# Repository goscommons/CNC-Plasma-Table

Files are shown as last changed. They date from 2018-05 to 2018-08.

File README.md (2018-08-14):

# CNC Plasma Cutter
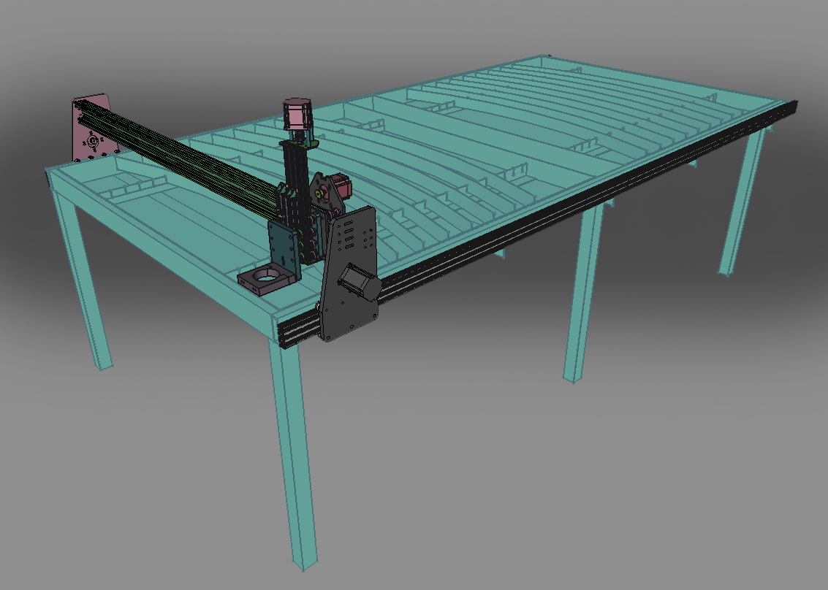
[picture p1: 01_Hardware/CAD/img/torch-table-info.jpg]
Name of the machine

## Purpose of the machine
Many fabricators use plasma arc cutting torches every day, either to replace or complement saws, cut-off wheels, snips, and oxyfuel rigs. Fabricators say the use of this equipment has grown because it can be used in a variety of applications, from installing heating, ventilation, air conditioning, refrigeration, and plumbing systems, to demolishing old industrial wash systems and erecting new ones, to cutting shapes to repair excavator booms or consistently cutting shapes.([Retrieved from the fabricator.com](https://www.thefabricator.com/article/plasmacutting/cut-it-out-how-fabricators-use-plasma-cutters-every-day))
## How the machine works
Plasma cutting is a process that cuts through electrically conductive materials by means of an accelerated jet of hot plasma. Typical materials cut with a plasma torch include steel, Stainless steel, aluminum, brass and copper, although other conductive metals may be cut as well. Plasma cutting is often used in fabrication shops, automotive repair and restoration, industrial construction, and salvage and scrapping operations. Due to the high speed and precision cuts combined with low cost, plasma cutting sees widespread use from large-scale industrial CNC applications down to small hobbyist shops([Retrieved from Wikipedia](https://en.wikipedia.org/wiki/Plasma_cutting)).
### Functional diagram
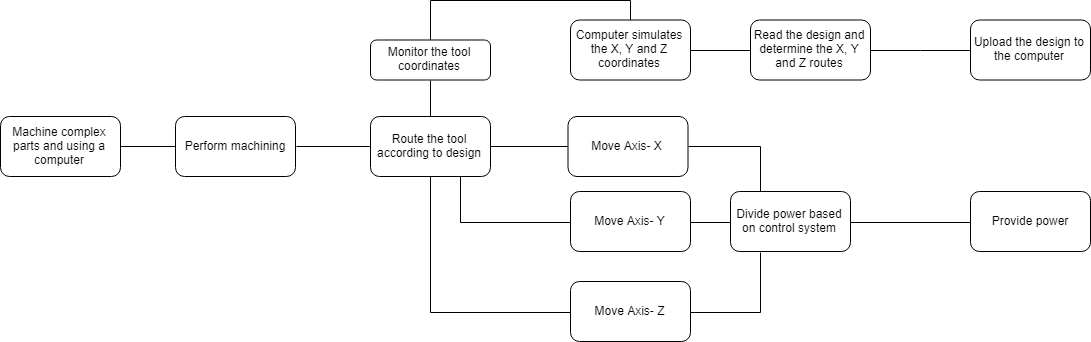
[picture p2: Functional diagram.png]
Fast Diagram- CNC plasma

## Use context
Plasma cutting is most widely used metal plate cutting processes for a large variety of industries. Early plasma cutting systems were used primarily for cutting stainless steel and aluminum plate from 0.5 to more than 6 in. thick. In the last 10 years, developments in plasma cutting technology have come at a fast pace with improved cut quality, automated gas flow control and the CAM software. The latest revision on high-definition machines is their full integration with the CNC machines they are coupled with.
## General specifications
The plasma cutting process needs clean air free of oil, parts and water vapor. The air compressors can leak oil, suck small particles, and they definitely condense water in the tank. Humidity in the compressed air shortens the life of the consumables of the torch. One way to get rig of the humidity is to install in line and air drying refrigerator unit, air filters, desiccants etc.
The one I made is a DIY and can get the job done with a fraction of the cost comparing similar characteristics. 
In general -more into details later-  a 4"PVC pipe right after the compressor exit -(not further downstream, but right after) filled with 1 gallon of reusable desiccant beads will hold all the moisture. The 4" diameter will slow down (bernoulli effect) the air so the beads it will have enough time to absorb the moisture. Also the cold air (due to the difference in pressure as it exits the tank) makes it easier to condense in that 4" pipe. For even better results in hot and humid climates the pipe could be installed in a refrigerator.

## References
1. [FAST diagram](http://www.valueanalysis.ca/fast.php)
2. [Technological evolution of Plasma cutting](https://www.thefabricator.com/article/plasmacutting/the-evolution-of-plasma-cutting)

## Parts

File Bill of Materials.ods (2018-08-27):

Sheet: current
item/part | CAD File | amount | unit | size/specs | cost per unit | shipping | total cost | remarks
Table frame (to be welded)
posts (50*50*3 square steel profile tubes) |  | 6 |  | 3*50*50*800 mm
sides short (25*75*3 rectangular steel profile tubes) |  | 2 |  | 3*25*75*1400 mm
sides long (25*75*3 rectangular steel profile tubes) |  | 2 |  | 3*25*75*3000 mm
cross supports (L profile) |  | 5 |  | (20*20*3)*1455
Water table (simple)
bottom sheet |  | 2 |  | 1400*1400*2 mm
sides (buy 2, cut in half) |  | 2 |  | 2800*75*2 mm
grid holders (T profile Alu with cuts) |  | 4 |  | (25*25*2)*1350 |  |  | Can also be L profile
grid (cutted sheet metal) |  | 18 |  | 20*2*1300
Y-axis (long)
Y-rails linear 20X60 V-slot profile |  | 4 |  | 1500*20*60 mm
timing belt |  | 2 |  | 3100 mm T2.5
timing belt pulley |  | 2 |  | T2.5 |  |  | can be 3D printed if needed.
Stepper motors |  | 2 |  | NEMA23
Y gantry plate |  | 2 |  | from DXF
bearing |  | 2 |  | 625ZZ
M5 lock nuts |  | 8 |  | M5 DIN985
M5 washers |  | 8 |  | M5 DIN 125A
M5 bolts (for motor) |  | 8 |  | M5x30
slide-in nut (to fasten timing belt) |  | 4 |  | ISB type 5- M4
M4 bolts |  | 4 |  | M4*25
screws (to fasten rails to frame) |  | 10
Wheel modules top |  | 8
wheel |  | 1 |  | 23 mm outer
matching ball bearing |  | 1 |  | 5 mm inner
M5 lock nut |  | 1 |  | M5 DIN 985
M5 washer |  | 4 |  | M5 DIN 125A
Spacer |  | 1 |  | 6mm M5
M5 bolt |  | 1 |  | 35 mm / DIN933
Wheel modules below |  | 6
wheel |  | 1 |  | 23 mm outer
matching ball bearing |  | 1 |  | 5 mm inner
M5 lock nut |  | 1 |  | M5 DIN 985
M5 washer |  | 4 |  | M5 DIN 125A
Eccentric spacer |  | 1 |  | 6mm M5
M5 bolt |  | 1 |  | 35 mm / DIN933
X-axis (short/moving)
linear cross bar (40x40 mm T-slot profile) |  | 1 |  | 40*40*1500 mm
M8 Bolts (to fasten cross bar to Y gantry) |  | 2 |  | M8*50
M8 washers |  | 2 |  | M8 DIN 125A
40x80 mm double v-slot U profile rail |  | 1 |  | 40*40*1500 mm
M5 Bolts (to fasten rails to Y gantry) |  | 8 |  | 35 mm / DIN933
M5 washers |  | 8 |  | M5 DIN 125A
timing belt |  | 1 |  | 1600 mm T2.5
slide-in nut (to fasten timing belt) |  | 2 |  | ISB type 5- M4
M4 bolts |  | 2 |  | M4*25
X gantry
X gantry plate front |  | 1 |  | from DXF
X gantry plate back |  | 1 |  | from DXF
Stepper motor |  | 1 |  | Nema23
timing belt pulley |  | 1 |  | T2.5
M5 bolts (for motor) |  | 4 |  | M3x30
M5 lock nuts |  | 4 |  | M3 DIN985
M5 washers |  | 4 |  | M3 DIN 125A
Double wheel modules top |  | 2
wheel |  | 2 |  | 23 mm outer
matching ball bearing |  | 2 |  | 5 mm inner
M5 lock nut |  | 1 |  | M5 DIN 985
M5 washer |  | 9 |  | M5 DIN 125A
Spacer |  | 3 |  | 6mm M5
M5 bolt |  | 1 |  | 35 mm / DIN933
Double wheel modules bottom |  | 2
wheel |  | 2 |  | 23 mm outer
matching ball bearing |  | 2 |  | 5 mm inner
M5 lock nut |  | 1 |  | M5 DIN 985
M5 washer |  | `9 |  | M5 DIN 125A
Eccentric spacer |  | 4 |  | 6mm M5
Spacer |  | 1 |  | 6mm M5
M5 bolt |  | 1 |  | 35 mm / DIN933
nut block for lead screw (anti backlash) |  | 1 |  | 8 screw thread
spacerblocks |  | 2 |  | from STL |  |  | It can be stronge enough from 3D printed PLA right? Otherwise: https://iprototype.nl/products/accessoires/construction/v-slot-spacerblock
Wheel module Z-axis eccentric |  | 4
wheel |  | 1 |  | 23 mm outer
matching ball bearing |  | 1 |  | 5 mm inner
M5 lock nut |  | 1 |  | M5 DIN 985
M5 washer |  | 2 |  | M5 DIN 125A
Eccentric spacer |  | 1 |  | 6mm M5
M5 bolt |  | 1 |  | 35 mm / DIN933
Wheel module Z-axis normal |  | 4
wheel |  | 1 |  | 23 mm outer
matching ball bearing |  | 1 |  | 5 mm inner
M5 lock nut |  | 1 |  | M5 DIN 985
M5 washer |  | 2 |  | M5 DIN 125A
Spacer |  | 1 |  | 6mm M5 |  |  | Shown as eccentric spacers in the CAD file. Needs to be adjusted.
M5 bolt |  | 1 |  | 35 mm / DIN933
Z-axis and gantry
Z-rail 20x60N-O aluminium T-slot profile |  | 1 |  | 20x60x280 mm
horizontal Z gantry plates |  | 2 |  | from DXF
Stepper motor |  | 1 |  | Nema23
Flexible coupling |  | 1 |  | 6,35/8 mm
Lead screw TR8X2 |  | 1 |  | 8*30 mm
Bearing |  | 2 |  | 608ZZ
Lock collar |  | 2 |  | 8 mm
M5 bolt |  | 3 |  | 50
Spacer |  | 3 |  | 40 mm
screws (plates to profile) |  | 6 |  | m5x20
Z-rail 20x60N-O aluminium T-slot profile |  | 1 |  | 20x60x150 mm |  |  | can be cut from a larger rail instead of ordering separate.
90 degrees corner bracket |  | 4 |  | for 20x20 profile
9 mm spacers |  | 4 |  | 9 mm
Mounting plate |  | 1 |  | 3D printed part
Wheel module Z-axis eccentric |  | 3
wheel |  | 1 |  | 23 mm outer
matching ball bearing |  | 1 |  | 5 mm inner
M5 lock nut |  | 1 |  | M5 DIN 985
M5 washer |  | 2 |  | M5 DIN 125A
Eccentric spacer |  | 1 |  | stock
M5 bolt |  | 1 |  | 35 mm / DIN933
Wheel module Z-axis normal |  | 3
wheel |  | 1 |  | 23 mm outer
matching ball bearing |  | 1 |  | 5 mm inner
M5 lock nut |  | 1 |  | M5 DIN 985
M5 washer |  | 2 |  | M5 DIN 125A
Spacer |  | 1 |  | 5,3*10*5 mm
M5 bolt |  | 1 |  | 35 mm / DIN933

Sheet: redesign
item/part | CAD File | amount | unit | size/specs | cost per unit | shipping | total cost | link to store (DUTCH) | remarks
 |  |  |  |  |  |  | €973,64 |  | shipping included?
Table frame
posts (40x40 mm T-slot profile) |  | 6 | ea | 40*40*800 mm | 14,03 |  | €84,18 | https://www.techniek-specialist.nl/aluminiumprofielen-specialist/isb-aluminium-profiel-40x40-eco/
sides short (40x40 mm T-slot profile) |  | 2 | ea | 40*40*1500 mm | 23,94 |  | €47,88 | https://www.techniek-specialist.nl/aluminiumprofielen-specialist/isb-aluminium-profiel-40x40-eco/
sides long (40x40 mm T-slot profile) |  | 2 | ea | 40*40*2000 mm | 31,02 |  | €62,04 | https://www.techniek-specialist.nl/aluminiumprofielen-specialist/isb-aluminium-profiel-40x40-eco/
corner fasteners big |  | 4 | ea | stock | €5,57 |  | €22,28 | https://reprapworld.nl/products/mechanical/frame_components/hoekverbinding_30x60_frame_groot/ | UPDATE
corner fasteners small |  | 12 | ea | stock | €3,25 |  | €39,00 | https://reprapworld.nl/products/mechanisch/frame_onderdelen/hoek_connector_30x30_frame_klein/ | Can also be all big fasteners
cross supports (L profile Alu) |  | 4 | ea | (20*20*2)*1040 | - |  |  | https://metaalcenter.nl/aluminium/aluminium-hoek-profiel/aluminium-hoekprofiel-20-x-20-x-2-mm.html
screws for supports (M5) |  | 8 | ea | stock | €0,12 |  | €0,96 | https://reprapworld.nl/products/mechanical/screws_nuts_and_washers/screws/hex/schroef_m5x20_hex/ | UPDATE
slide nuts for supports (M5) |  | 8 | ea | stock | 6,53/20 pcs |  | €6,53 | https://reprapworld.nl/products/mechanisch/schroeven_moeren_en_ringen/moeren/t_slots/slide_nut_m5_fro_30x30_extrusions_20_pieces/ | UPDATE
rings for supports (M5) |  | 8 | ea | stock | 0,04 |  | €0,32 | https://reprapworld.nl/products/mechanical/screws_nuts_and_washers/washers/sluitring_m5_normaal/ | UPDATE
Water table (simple)
bottom sheet |  | 1 | ea | 2000*1000*2 mm | 58,3 |  | €58,30 | https://metaalcenter.nl/aluminium/aluminium-plaat/aluminium-plaat2000-x-1000-x-2-mm.html | CHECK SIZES FOR 2*1,5 m
sides (sheets, later 1 cut in half) |  | 3 | ea | 2000*30*2 mm | - |  | €21,78 | https://metaalcenter.nl/aluminium/aluminium-plat/aluminium-platstaf-30-x-2-mm.html
grid holders (T profile Alu with cuts) |  | 3 | ea | (25*25*2)*1970 | - |  | €26,13 | https://metaalcenter.nl/aluminium/aluminium-hoek-profiel/aluminium-hoekprofiel-20-x-20-x-2-mm.html | Can also be L profile
grid |  | 11 | ea | 20*2*1000 | - |  | €38,72 | https://metaalcenter.nl/aluminium/aluminium-plat/aluminium-platstaf-20-x-2-mm.html
Y-axis (long)
Y-rails linear 20X60 profile |  | 2 | ea | 2000*20*60 mm | 45,54 |  | €91,08 | https://www.techniek-specialist.nl/aluminiumprofielen-specialist/isb-aluminium-profiel-60x20n-o/ | of https://openbuildspartstore.com/v-slot-20x60-linear-rail/
timing belt |  | 2 | ea | 2100 mm T2.5 | 3,03 |  | €6,06 | https://reprapworld.nl/products/lineaire_beweging/distributieriem_1m_x_5mm_2_5mm_pitch_t2_5/
timing belt pulley |  | 2 | ea | T2.5 | 3,01 |  | €6,02 | https://reprapworld.nl/products/mechanisch/pulleys/aluminium_tandriemschijf_t2_5/ | can be 3D printed if needed.
Stepper motors |  | 2 | ea | - | 12,09 |  | €24,18 | https://reprapworld.nl/products/motors_fans/stepper_motors/nema17_stappenmotor_1_8_stap_4_08_kg_cm/ | Is the torque high enough? Can take the NEMA23: https://reprapworld.nl/products/motoren_fans/stepper_motors/nema23_stepper_motor_1_8_step_12_85_kg_cm/
Y gantry plate |  | 2 | ea | from DXF | - |  |  | Build with DFX file | DXF needs to be adjusted
bearing |  | 2 | ea | 625ZZ | 0,42 |  | €0,84 | https://reprapworld.nl/products/mechanical/bearings/afgeschermde_kogellager_625zz/
M3 lock nuts |  | 8 | ea | M3 DIN985 | 0,04 |  | €0,32 | https://reprapworld.nl/products/mechanisch/schroeven_moeren_en_ringen/moeren/nylon_slot/moer_m3_borgmoer/
M3 washers |  | 8 | ea | M3 DIN 125A | 0,04 |  | €0,32 | https://reprapworld.nl/products/mechanisch/schroeven_moeren_en_ringen/sluitringen/sluitring_m3_normaal/
M3 bolts (for motor) |  | 8 | ea | M3x30 | 0,15 |  | €1,20 | https://reprapworld.nl/products/mechanical/screws_nuts_and_washers/screws/hex/schroef_m3x30_hex/
slide-in nut (to fasten timing belt) |  | 4 | ea | ISB type 5- M4 | 0,22 |  | €0,88 | https://www.techniek-specialist.nl/aluminiumprofielen-specialist/t-sleuf-inschuifmoer/
M4 bolts |  | 4 | ea | M4*25 | 0,12 |  | €0,48 | https://reprapworld.nl/products/mechanical/screws_nuts_and_washers/screws/hex/schroef_m4x25_hex/
slide-in nut (to fasten rails to frame) |  | 10 | ea | ISB type 5- M4 | 0,22 |  | €2,20 | https://www.techniek-specialist.nl/aluminiumprofielen-specialist/t-sleuf-inschuifmoer/
M4 bolts |  | 10 | ea | M4*25 | 0,12 |  | €1,20 | https://reprapworld.nl/products/mechanical/screws_nuts_and_washers/screws/hex/schroef_m4x25_hex/
Wheel modules |  | 14 |  |  |  |  | €40,53
wheel |  | 1 | ea | 23 mm outer | 2,72 |  |  | https://reprapworld.nl/products/mechanisch/kogellagers/625zz_shielded_ball_bearing_23_mm_nylon_wheel/ | CHECK WHETHER THIS IS CHEAPER: https://openbuildspartstore.com/solid-v-wheel-kit/
bearing included |  | 1 | ea | 5 mm inner | -
M5 lock nut |  | 1 | ea | M5 DIN 985 | 0,04 |  |  | https://reprapworld.nl/products/mechanical/screws_nuts_and_washers/nuts/nylon_lock/moer_m5_borgmoer/
M5 washer |  | 4 | ea | M5 DIN 125A | 0,04 |  |  | https://reprapworld.nl/products/mechanical/screws_nuts_and_washers/washers/sluitring_m5_normaal/
Spacer |  | 1 | ea | 5,3*10*5 mm | 0,22 |  |  | https://www.mparts.nl/afstandsbus-rond-ca0158020500 | or https://openbuildspartstore.com/aluminum-spacers-10-pack/
M5 bolt |  | 1 | ea | 35 mm / DIN933 | 0,1 |  |  | https://www.zamro.nl/product/81E0C/d933-rvs-a2-tapbout-m5x35-200
X-axis (short/moving)
linear cross bar (40x40 mm T-slot profile) |  | 1 | ea | 40*40*1500 mm | 23,94 |  | €23,94 | https://www.techniek-specialist.nl/aluminiumprofielen-specialist/isb-aluminium-profiel-40x40-eco/ | I this really needed? Can't it be a thinner profile? For instance a flat 40x20 profile: https://www.techniek-specialist.nl/aluminiumprofielen-specialist/isb-aluminium-profiel-20x40n-o/
M8 Bolts (to fasten cross bar to Y gantry) |  | 2 | ea | M8*50 | 0,22 |  | €0,44 | https://reprapworld.nl/products/mechanisch/schroeven_moeren_en_ringen/schroeven/philips/schroef_m8x30_philips/
M8 washers |  | 2 | ea | M8 DIN 125A | 0,04 |  | €0,08 | https://reprapworld.nl/products/mechanical/screws_nuts_and_washers/washers/sluitring_m8_normaal/
2X 40x40 mm double T-slot profile rail |  | 2 | ea | 40*40*1500 mm | 26,48 |  | €52,96 | https://www.techniek-specialist.nl/aluminiumprofielen-specialist/isb-aluminium-profiel-40x40n-o/ | This is different from the other rails, it has two 20 mm T-slot profile rails next to eachother.
M5 Bolts (to fasten rails to Y gantry) |  | 8 | ea | 35 mm / DIN933 | 0,1 |  | €0,80 | https://www.zamro.nl/product/81E0C/d933-rvs-a2-tapbout-m5x35-200 | included in big pack
M5 washers |  | 8 | ea | M5 DIN 125A | 0,04 |  | €0,32 | https://reprapworld.nl/products/mechanical/screws_nuts_and_washers/washers/sluitring_m5_normaal/
timing belt |  | 1 | ea | 1600 mm T2.5 | 3,03 |  | €3,03 | https://reprapworld.nl/products/lineaire_beweging/distributieriem_1m_x_5mm_2_5mm_pitch_t2_5/
slide-in nut (to fasten timing belt) |  | 2 | ea | ISB type 5- M4 | 0,22 |  | €0,44 | https://www.techniek-specialist.nl/aluminiumprofielen-specialist/t-sleuf-inschuifmoer/
M4 bolts |  | 2 | ea | M4*25 | 0,12 |  | €0,24 | https://reprapworld.nl/products/mechanical/screws_nuts_and_washers/screws/hex/schroef_m4x25_hex/
X gantry
X gantry plate front |  | 1 | ea | from DXF | - |  |  | lasercut updated dxf | DXF needs to be adjusted
X gantry plate back |  | 1 | ea | from DXF | - |  |  | lasercut updated dxf | DXF needs to be adjusted
Stepper motors |  | 1 | ea | - | 12,09 |  | €12,09 | https://reprapworld.nl/products/motors_fans/stepper_motors/nema17_stappenmotor_1_8_stap_4_08_kg_cm/ | Is the torque high enough? Can take the NEMA23: https://reprapworld.nl/products/motoren_fans/stepper_motors/nema23_stepper_motor_1_8_step_12_85_kg_cm/
timing belt pulley |  | 1 | ea | T2.5 | 3,01 |  | €3,01 | https://reprapworld.nl/products/mechanisch/pulleys/aluminium_tandriemschijf_t2_5/
M3 bolts (for motor) |  | 4 | ea | M3x30 | 0,15 |  | €0,60 | https://reprapworld.nl/products/mechanical/screws_nuts_and_washers/screws/hex/schroef_m3x30_hex/
M3 lock nuts |  | 4 | ea | M3 DIN985 | 0,04 |  | €0,16 | https://reprapworld.nl/products/mechanisch/schroeven_moeren_en_ringen/moeren/nylon_slot/moer_m3_borgmoer/
M3 washers |  | 4 | ea | M3 DIN 125A | 0,04 |  | €0,16 | https://reprapworld.nl/products/mechanisch/schroeven_moeren_en_ringen/sluitringen/sluitring_m3_normaal/
Double wheel modules top |  | 2 |  |  |  |  | €13,64
wheel |  | 2 | ea | 23 mm outer | 2,72 |  |  | https://reprapworld.nl/products/mechanisch/kogellagers/625zz_shielded_ball_bearing_23_mm_nylon_wheel/
bearing included |  | 2 | ea | 5 mm inner | -
M5 lock nut |  | 1 | ea | M5 DIN 985 | 0,04 |  |  | https://reprapworld.nl/products/mechanical/screws_nuts_and_washers/nuts/nylon_lock/moer_m5_borgmoer/
M5 washer |  | 9 | ea | M5 DIN 125A | 0,04 |  |  | https://reprapworld.nl/products/mechanical/screws_nuts_and_washers/washers/sluitring_m5_normaal/
Spacer |  | 4 | ea | 5,3*10*5 mm | 0,22 |  |  | https://www.mparts.nl/afstandsbus-rond-ca0158020500
M5 bolt |  | 1 | ea | 35 mm / DIN933 | 0,1 |  |  | https://www.zamro.nl/product/81E0C/d933-rvs-a2-tapbout-m5x35-200 | Depends on the thickness of the plates. This will do up to 3 mm thickness.
Double wheel modules bottom |  | 2 |  |  |  |  | €31,00
wheel |  | 2 | ea | 23 mm outer | 2,72 |  |  | https://reprapworld.nl/products/mechanisch/kogellagers/625zz_shielded_ball_bearing_23_mm_nylon_wheel/
bearing included |  | 2 | ea | 5 mm inner | -
M5 lock nut |  | 1 | ea | M5 DIN 985 | 0,04 |  |  | https://reprapworld.nl/products/mechanical/screws_nuts_and_washers/nuts/nylon_lock/moer_m5_borgmoer/
M5 washer |  | 7 | ea | M5 DIN 125A | 0,04 |  |  | https://reprapworld.nl/products/mechanical/screws_nuts_and_washers/washers/sluitring_m5_normaal/
Eccentric spacer |  | 4 | ea | stock | 2,3 |  |  | https://iprototype.nl/products/accessoires/construction/v-slot-eccentric-spacer
Spacer |  | 2 | ea | 5,3*10*5 mm | 0,22 |  |  | https://www.mparts.nl/afstandsbus-rond-ca0158020500
M5 bolt |  | 1 | ea | 35 mm / DIN933 | 0,1 |  |  | https://www.zamro.nl/product/81E0C/d933-rvs-a2-tapbout-m5x35-200 | Depends on the thickness of the plates. This will do up to 3 mm thickness.
nut block for lead screw (anti backlash) |  | 1 |  | 8 screw thread |  |  | €10,44 | http://vslot-europe.com/home/64-anti-backlash-nut-block-for-8mm-metric-acme-lead-screw.html | Without anti-backlash arm is cheaper and can be bought with other parts: https://iprototype.nl/products/accessoires/construction/8mm-acme-nut-block
spacerblocks |  | 2 |  | from STL |  |  |  | 3D print from STL | It can be stronge enough from 3D printed PLA right? Otherwise: https://iprototype.nl/products/accessoires/construction/v-slot-spacerblock
Wheel module Z-axis eccentric |  | 4 |  |  |  |  | €20,96
wheel |  | 1 |  | 23 mm outer | 2,72 |  |  | https://reprapworld.nl/products/mechanisch/kogellagers/625zz_shielded_ball_bearing_23_mm_nylon_wheel/
bearing included |  | 1 |  | 5 mm inner | -
M5 lock nut |  | 1 |  | M5 DIN 985 | 0,04 |  |  | https://reprapworld.nl/products/mechanical/screws_nuts_and_washers/nuts/nylon_lock/moer_m5_borgmoer/
M5 washer |  | 2 |  | M5 DIN 125A | 0,04 |  |  | https://reprapworld.nl/products/mechanical/screws_nuts_and_washers/washers/sluitring_m5_normaal/
Eccentric spacer |  | 1 |  | stock | 2,3 |  |  | https://iprototype.nl/products/accessoires/construction/v-slot-eccentric-spacer
M5 bolt |  | 1 |  | 35 mm / DIN933 | 0,1 |  |  | https://www.zamro.nl/product/81E0C/d933-rvs-a2-tapbout-m5x35-200 | Check sizing for all bolts with eccentric spacers
Wheel module Z-axis normal |  | 4 |  |  |  |  | €12,64
wheel |  | 1 |  | 23 mm outer | 2,72 |  |  | https://reprapworld.nl/products/mechanisch/kogellagers/625zz_shielded_ball_bearing_23_mm_nylon_wheel/
bearing included |  | 1 |  | 5 mm inner | -
M5 lock nut |  | 1 |  | M5 DIN 985 | 0,04 |  |  | https://reprapworld.nl/products/mechanical/screws_nuts_and_washers/nuts/nylon_lock/moer_m5_borgmoer/
M5 washer |  | 2 |  | M5 DIN 125A | 0,04 |  |  | https://reprapworld.nl/products/mechanical/screws_nuts_and_washers/washers/sluitring_m5_normaal/
Spacer |  | 1 |  | 5,3*10*5 mm | 0,22 |  |  | https://www.mparts.nl/afstandsbus-rond-ca0158020500 | Shown as eccentric spacers in the CAD file. Needs to be adjusted.
M5 bolt |  | 1 |  | 35 mm / DIN933 | 0,1 |  |  | https://www.zamro.nl/product/81E0C/d933-rvs-a2-tapbout-m5x35-200
Z-axis and gantry
Z-rail 20x60N-O aluminium T-slot profile |  | 1 |  | 20x60x280 mm | €8,70 |  | €8,70 | https://www.techniek-specialist.nl/aluminiumprofielen-specialist/isb-aluminium-profiel-60x20n-o/
horizontal Z gantry plates |  | 2 |  | from DXF | - |  |  |  | Aren't there standard parts for this tht we can buy?
Stepper motor |  | 1 |  | Nema23 | 36,3 |  | €36,30 | https://reprapworld.nl/products/motoren_fans/stepper_motors/nema23_stepper_motor_1_8_step_12_85_kg_cm/
Flexible coupling |  | 1 |  | 6,35/8 mm | 4,22 |  | €4,22 | https://reprapworld.nl/products/motoren_fans/couplers/flexible_motor_coupling_6_35_mm_8_mm/
Lead screw TR8X2 |  | 1 |  | 8*30 mm | 9,56 |  | €9,56 | https://reprapworld.nl/products/lineaire_geleiding/spindel_tr8x2_8_mm_2_mm_per_rev_30_cm/
Bearing |  | 2 |  | 608ZZ | 0,75 |  | €1,50 | https://reprapworld.nl/products/mechanisch/kogellagers/afgeschermde_kogellager_608zz/
Lock collar |  | 2 |  | 8 mm | 1,44 |  | €2,88 | http://vslot-europe.com/home/51-lock-collar-8mm.html
M5 bolt |  | 3 |  | 50 |  |  | €3,39 | https://www.gamma.nl/assortiment/gamma-metaalschroef-m5-x-50mm-platkop-verzinkt-15-stuks/p/B458479 | Have to buy in set, nuts included
Spacer |  | 3 |  | 40 mm |  |  | €4,45 | https://iprototype.nl/products/accessoires/construction/v-slot-aluminium-spacer-20mm | cant find 40mm spacers, only when bought per 100 pcs, use 2x20 instead
screws (plates to profile) |  | 6 |  | m5x20 | €0,12 |  | €0,72 | https://reprapworld.nl/products/mechanical/screws_nuts_and_washers/screws/hex/schroef_m5x20_hex/
Z-rail 20x60N-O aluminium T-slot profile |  | 1 |  | 20x60x150 mm | €5,91 |  | €5,91 | https://www.techniek-specialist.nl/aluminiumprofielen-specialist/isb-aluminium-profiel-60x20n-o/ | can be cut from a larger rail instead of ordering separate.
90 degrees corner bracket |  | 4 |  | for 20x20 profile | 3,03 |  | €12,12 | https://reprapworld.nl/products/mechanisch/frame_onderdelen/hoekverbinding_klein_20x20_frame/
9 mm spacers |  | 4 |  | 9 mm | 2,95 /set |  | €2,95 | https://iprototype.nl/products/accessoires/construction/v-slot-aluminium-spacer-9mm
Mounting plate |  | 1 |  | 3D printed part | - |  | ? | These should probably be redesigned to fit the plasmacutter of choice
Wheel module Z-axis eccentric |  | 3 |  |  |  |  | €15,72
wheel |  | 1 |  | 23 mm outer | 2,72 |  |  | https://reprapworld.nl/products/mechanisch/kogellagers/625zz_shielded_ball_bearing_23_mm_nylon_wheel/
bearing included |  | 1 |  | 5 mm inner | -
M5 lock nut |  | 1 |  | M5 DIN 985 | 0,04 |  |  | https://reprapworld.nl/products/mechanical/screws_nuts_and_washers/nuts/nylon_lock/moer_m5_borgmoer/
M5 washer |  | 2 |  | M5 DIN 125A | 0,04 |  |  | https://reprapworld.nl/products/mechanical/screws_nuts_and_washers/washers/sluitring_m5_normaal/
Eccentric spacer |  | 1 |  | stock | 2,3 |  |  | https://iprototype.nl/products/accessoires/construction/v-slot-eccentric-spacer
M5 bolt |  | 1 |  | 35 mm / DIN933 | 0,1 |  |  | https://www.zamro.nl/product/81E0C/d933-rvs-a2-tapbout-m5x35-200 | Check sizing for all bolts with eccentric spacers
Wheel module Z-axis normal |  | 3 |  |  |  |  | €9,48
wheel |  | 1 |  | 23 mm outer | 2,72 |  |  | https://reprapworld.nl/products/mechanisch/kogellagers/625zz_shielded_ball_bearing_23_mm_nylon_wheel/
bearing included |  | 1 |  | 5 mm inner | -
M5 lock nut |  | 1 |  | M5 DIN 985 | 0,04 |  |  | https://reprapworld.nl/products/mechanical/screws_nuts_and_washers/nuts/nylon_lock/moer_m5_borgmoer/
M5 washer |  | 2 |  | M5 DIN 125A | 0,04 |  |  | https://reprapworld.nl/products/mechanical/screws_nuts_and_washers/washers/sluitring_m5_normaal/
Spacer |  | 1 |  | 5,3*10*5 mm | 0,22 |  |  | https://www.mparts.nl/afstandsbus-rond-ca0158020500 | Shown as eccentric spacers in the CAD file. Needs to be adjusted.
M5 bolt |  | 1 |  | 35 mm / DIN933 | 0,1 |  |  | https://www.zamro.nl/product/81E0C/d933-rvs-a2-tapbout-m5x35-200
Electronics (central)
Electric box |  | 1 | ea |  |  |  | €0,00 |  | Can be 3D printed
CNC Hat w/sockets for external drivers |  | 1 | ea |  |  |  | €0,00 | https://www.ebay.com/itm/Raspberry-Pi-CNC-Hat-V2-60-GRBL-v1-1-Compatible-Extra-Options/272596155477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 | Stick with grbl for now. I personally used the "CNC shield" over Arduino but I propose the "CNC Hat" over Raspberry Pi.
Raspberry Pi |  | 1 | ea |  | 40 |  | €40,00
Stepper Drivers TB6600 |  | 1 | 5pack |  | 25,64 | 3,72 | €29,36
wire |  | 20 | meter | 4pin 22awg | 0,8 |  | €16,00 |  | estimation on length
wires for raspberry Pi?? Power,VGA?
Monitor?
Torch Height Control |  | 1 | ea | Proma SD | 238 |  |  | http://proma-elektronika.com/index.php/en/products/thc-torch-height-control/compact-thc-sd

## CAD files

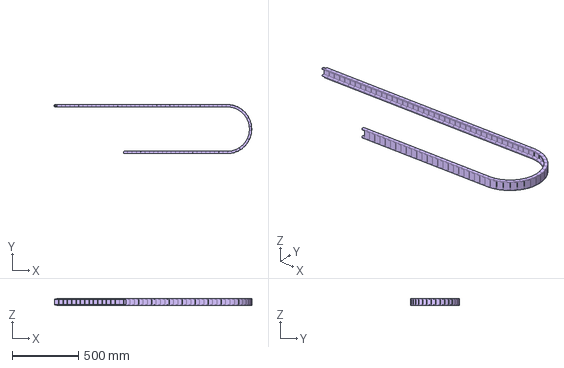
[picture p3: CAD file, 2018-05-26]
01_Hardware/CAD/Chain Assembly Y.fcstd
1491.6 x 371.6 x 49.6 mm

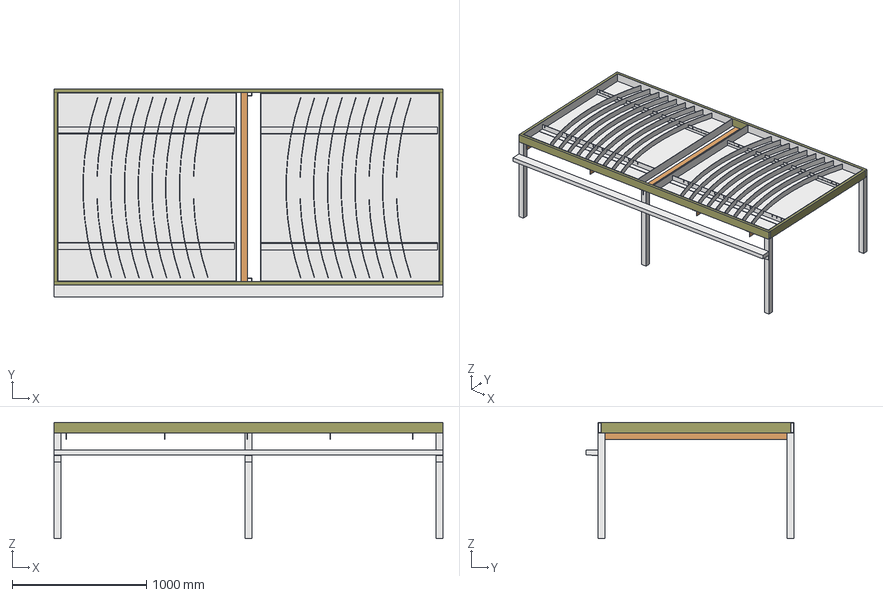
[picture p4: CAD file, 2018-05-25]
01_Hardware/CAD/frame assembly.fcstd
2895.6 x 1544.6 x 864.6 mm
frame sides_01
frame_water_table_cross_supports_01
frame posts_01
Water_table_Assembly_01
Water_table_Assembly_02
Drag_Chain_Y_Axis_Support_Module_01

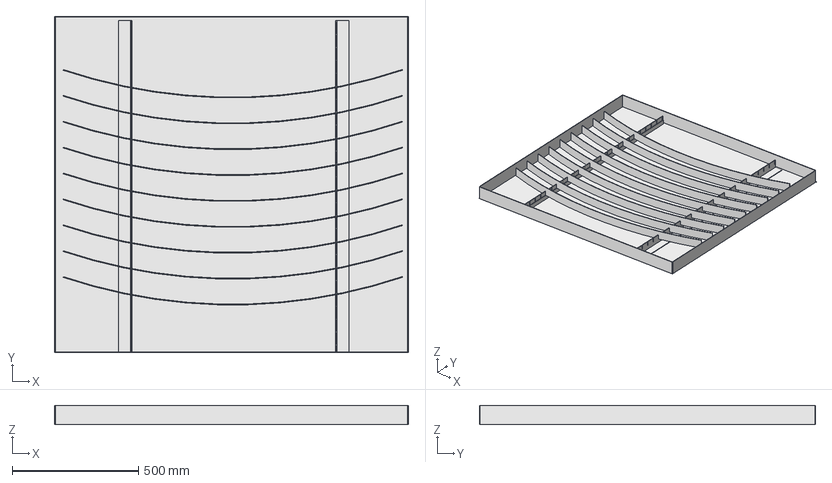
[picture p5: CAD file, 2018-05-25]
01_Hardware/CAD/Water table Assembly.fcstd
1403.3 x 1333.5 x 77.2 mm
water_table_pan_01
water_table_slat_support_01
water_table_slats_01
import_temporary_part

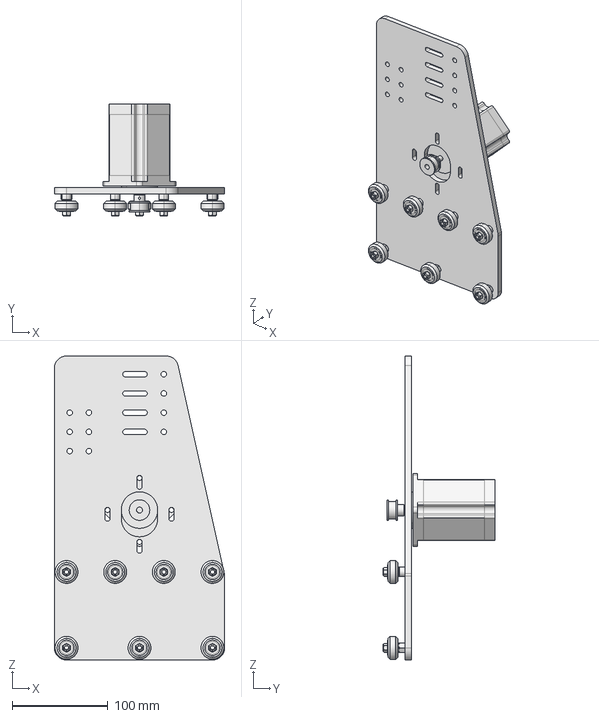
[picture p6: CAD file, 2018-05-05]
01_Hardware/CAD/Y axis gantry assembly MIRROR.fcstd
177.8 x 117.3 x 317.5 mm

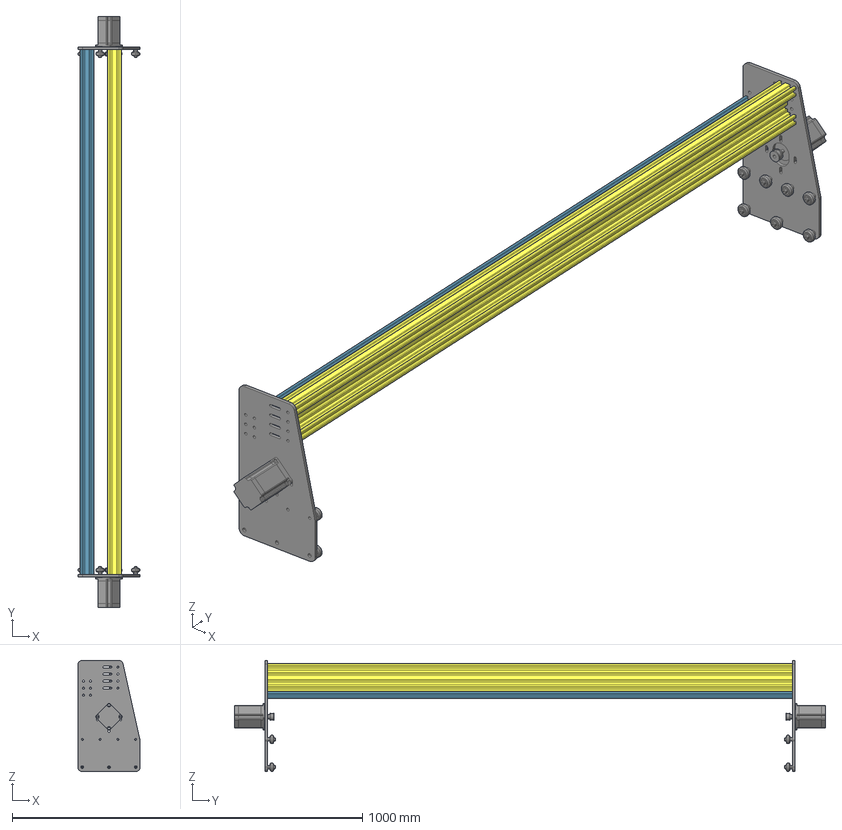
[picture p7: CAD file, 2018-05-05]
01_Hardware/CAD/Y Rail Assembly.fcstd
177.8 x 1687.8 x 317.5 mm
Y_axis_gantry_assembly_01
X Linear rail front
Y_axis_gantry_assembly_MIRROR_01
X Linear Rail Back

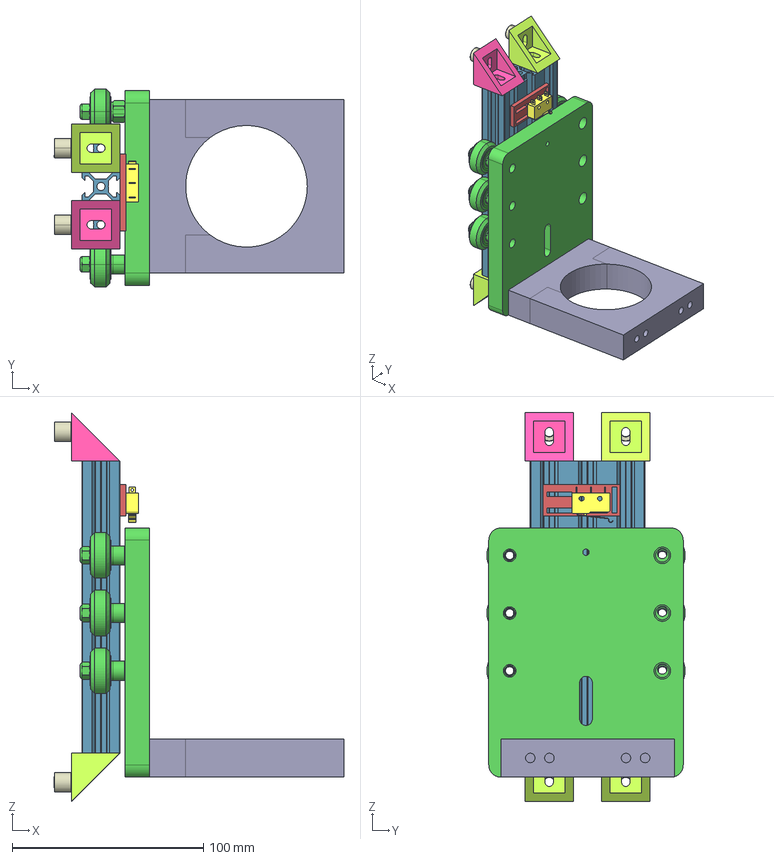
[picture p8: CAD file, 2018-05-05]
01_Hardware/CAD/Z Floating Assembly.fcstd
151.2 x 103.7 x 203.2 mm
Z_Linear_Rail_01
Cast_Corner_Bracket_step1_01
Cast_Corner_Bracket_step1_02
Cast_Corner_Bracket_step1_03
Cast_Corner_Bracket_step1_04
Micro_Limit_Switch_step1_01
End stop mounting plate
Floating_Plate_Module_01
Mount_Plate_02
Aluminum_Spacer_9mm_02
Aluminum_Spacer_9mm_03
Aluminum_Spacer_9mm_04
Aluminum_Spacer_9mm_01

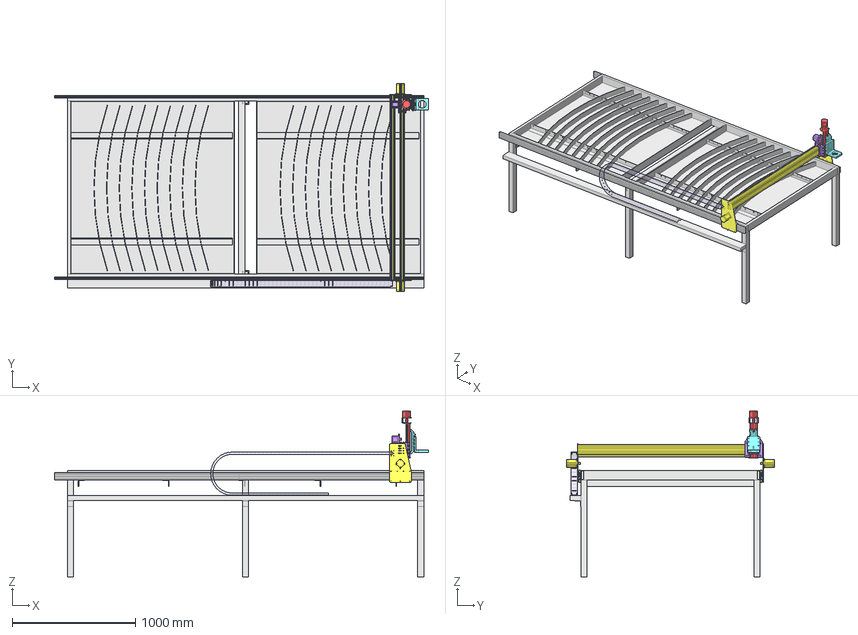
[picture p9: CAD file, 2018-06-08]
01_Hardware/CAD/CNC Master CAD_REMOTE_5589.fcstd
3038.0 x 1687.8 x 1348.3 mm
frame_assembly_01
Y_Linear_Rails_01
X_gantry_01
Y_Rail Assembly
Z_Axis_01
Y_Linear_Rails_02
Z_Floating_Assembly_01001
Chain_Assembly_Y_01

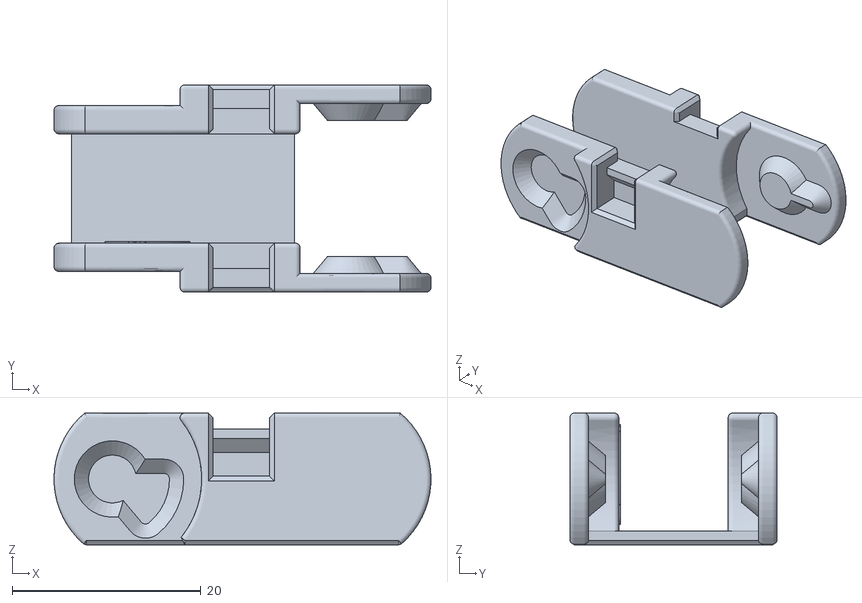
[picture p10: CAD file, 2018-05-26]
01_Hardware/stl-files/UM2CableChain_ChainSegment.STL
40.0 x 22.0 x 14.0

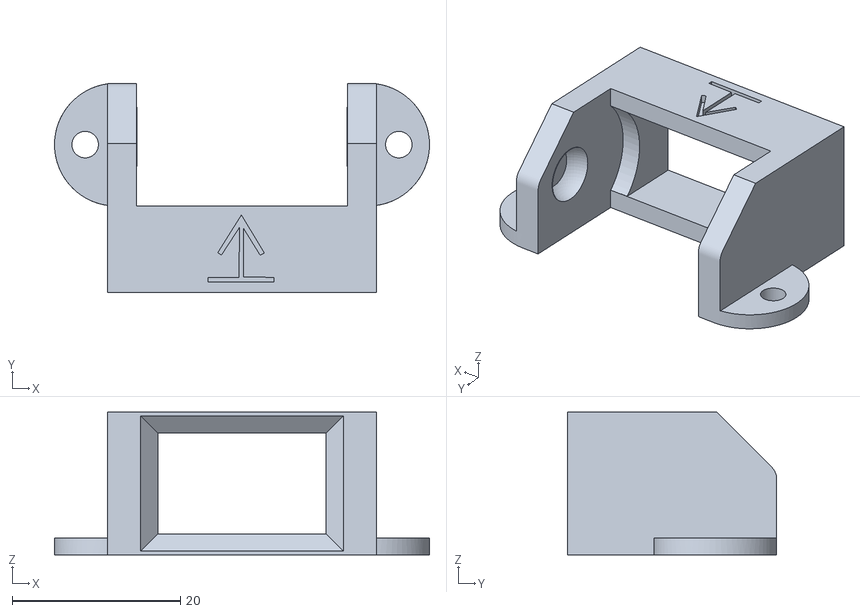
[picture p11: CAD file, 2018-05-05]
01_Hardware/stl-files/HD_Drag_Chain_Start_V2.stl
44.6 x 24.9 x 17.0

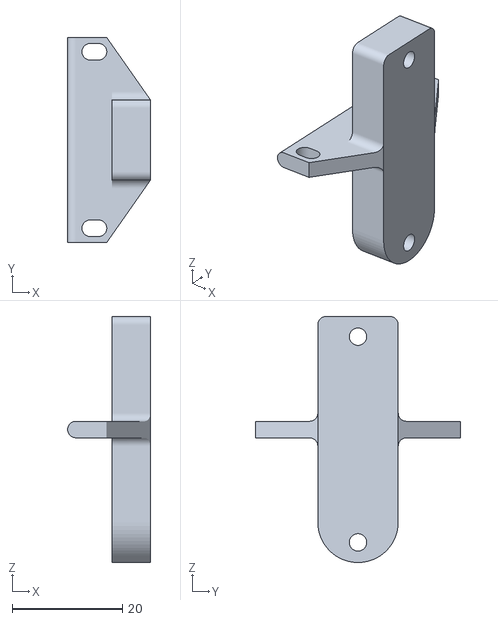
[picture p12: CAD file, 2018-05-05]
01_Hardware/stl-files/N23_Mnt.stl
15.0 x 37.2 x 44.6

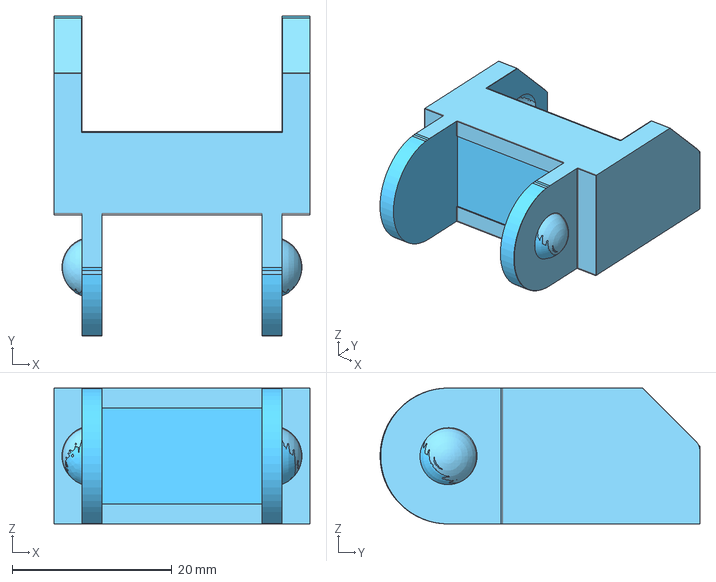
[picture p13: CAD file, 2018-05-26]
01_Hardware/CAD/HD_Drag_Chain_End_V2.FCStd
32.0 x 40.0 x 17.0 mm
HD_Drag_Chain_V2

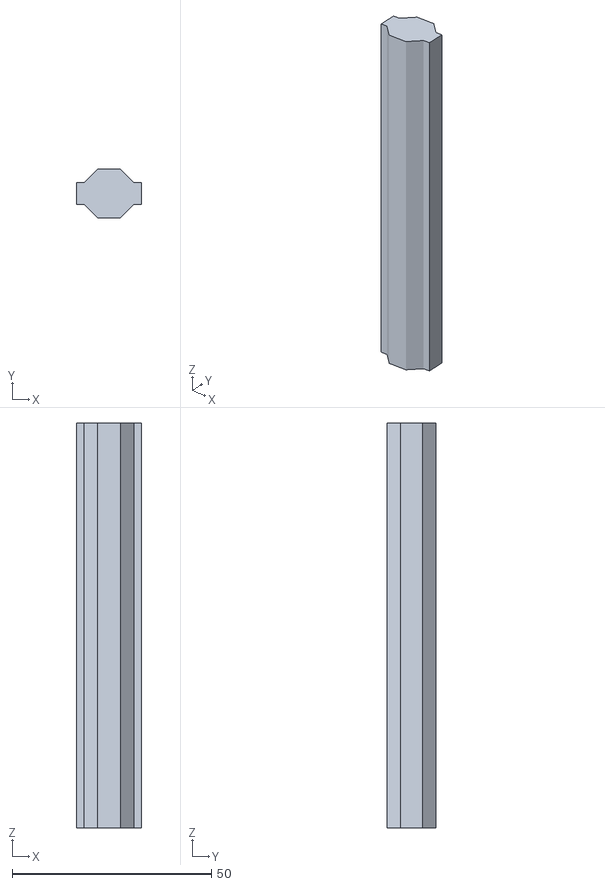
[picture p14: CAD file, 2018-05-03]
01_Hardware/stl-files/rail connector.stl
16.4 x 12.2 x 101.6

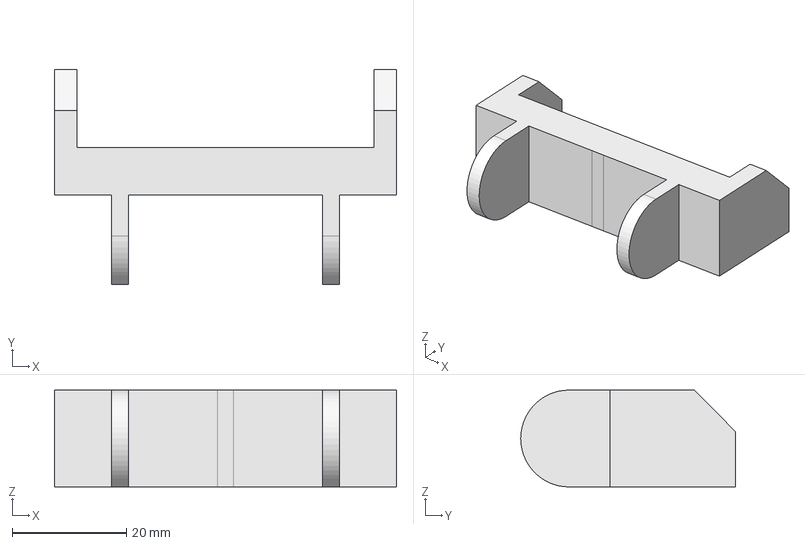
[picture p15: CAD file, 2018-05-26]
01_Hardware/CAD/HD_drag_Chain_V2.FCStd
60.0 x 37.7 x 17.0 mm

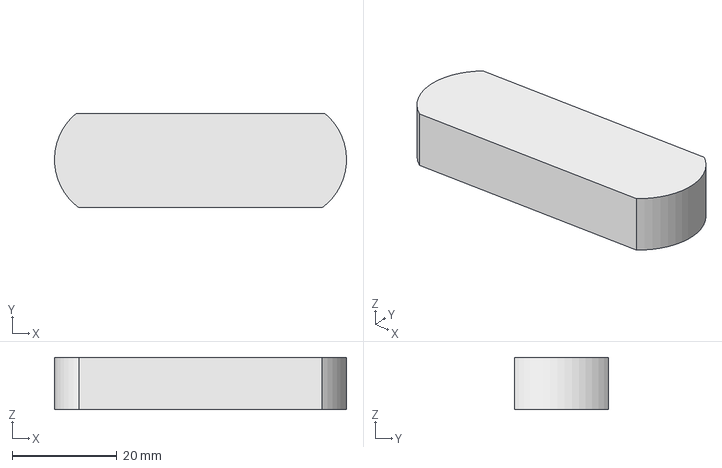
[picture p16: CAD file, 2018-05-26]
01_Hardware/CAD/Cable-chain-chain-segment.FCStd
55.6 x 18.0 x 10.0 mm

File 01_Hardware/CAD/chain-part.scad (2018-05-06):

/* module body(){
	cube()
} */

 cube([18,28,8],true);

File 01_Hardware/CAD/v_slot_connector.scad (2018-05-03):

/*
///////////////////////////////////////////////////////////////////////////////////
// Open SCAD Notes
% = background : # = debug : ! = root : * = disable

union() : intersection() : difference() : minkowski() :hull()
translate([X, Y, Z]) : rotate([X,Y,Z]) : scale([x, y, z])
linear_extrude(height = X, center = true, convexity = 10, twist = Y, slices = 20)

square ([X,Y],center = true) : cube([X, Y, Z], center=true)
circle(r = X) : cylinder(r1=X, r2=Y, h=Z, center=true, $fn=20) : sphere(2, $fn=100)
color("Red",0.7)

polygon(points=[[-50,0],[-50,50],[50,50],[50,0]], paths=[[0,1,2,3]]);
polyhedron(points=[[-50,0],[-50,50],[50,50],[50,0], triangles=[[1,0,3],[2,1,3]]);

// STL Import
translate([0, 0, 0])
import("OpenBeam.stl");

///////////////////////////////////////////////////////////////////////////////////
*/

include <metric_fastners.scad>;


scale = 0.99;
length = 40;


module beam(length=40) {
	linear_extrude(length)
	 polygon([ [-4.5, 0], [-2.7, -1.9], [-5.5,-1.9], [-5.5, -2.8], [-3, -5.7], [3, -5.7], [5.5, -2.8], [5.5,-1.9], [2.7, -1.9], [4.5, 0], [2.7, 1.9], [5.5, 1.9], [5.5, 2.8], [3, 5.7], [-3, 5.7], [-5.5, 2.8], [-5.5,1.9], [-2.7, 1.9] ]);
}


module connector() {
	difference() {
	translate([0, 0, -length/2]) rotate([0, 0, 0]) scale([scale, scale, scale])
 	 beam(length);

*#	translate([0, 2, 0]) rotate([90, 0, 0])
		 cap_bolt_boolean(3, 8, 30);
	}
}



// Primary Placement
translate([0, 0, 0]) rotate([0, 0, 0])
connector(40);

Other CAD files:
01_Hardware/CAD/Y axis gantry assembly.fcstd
01_Hardware/CAD/CNC Master CAD.fcstd
01_Hardware/CAD/Cable-chain-segment.FCStd
01_Hardware/CAD/Drag Chain Y Axis Support Angles.fcstd
01_Hardware/CAD/20 x 40 linear rail Z.fcstd
01_Hardware/CAD/8mm Leadscrew Acme 12in.fcstd
01_Hardware/CAD/Aluminum Spacer .25in.step
01_Hardware/CAD/Aluminum Spacer 20mm.fcstd
01_Hardware/CAD/Aluminum Spacer 9mm.fcstd
01_Hardware/CAD/Aluminum Spacer 9mm.step
01_Hardware/CAD/C beam X rail.fcstd
01_Hardware/CAD/CNC Master CAD_BACKUP_5589.fcstd
01_Hardware/CAD/CNC Master CAD_BASE_5589.fcstd
01_Hardware/CAD/CNC Master CAD_LOCAL_5589.fcstd
01_Hardware/CAD/Drag Chain Y Axis Support Beam.fcstd
01_Hardware/CAD/Drag Chain Y Axis Support Module.fcstd
01_Hardware/CAD/Eccentric Spacer 0.25in.step
01_Hardware/CAD/Floating Plate Module.fcstd
01_Hardware/CAD/Floating Plate.fcstd
01_Hardware/CAD/GT3 Timing Pulley 20T.fcstd
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

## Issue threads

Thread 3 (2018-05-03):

Unused files should be deleted. File tree diagram needed

polemidis, 2018-05-03:
lots of files are not used anymore. One has to open all the sub-assemblies and modules to see what is not used anymore, as find any files that may be missing. (Most likely missing file will be OpenBuillds© cad models).

jurra, 2018-05-22:
This can be closed right?

polemidis, 2018-05-22:
No yet. There is a mess in the files. We need to make a tree diagram (like the one for the grapple) and then  keep the needed files. Most likely there will be deprecated files there.

jurra, 2018-05-22:
Ok I understand

On Tue, May 22, 2018, 12:18 Manolis Karamousas <notifications@github.com>
wrote:

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

Closed 2018-08-21.

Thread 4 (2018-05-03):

The gantry plates have inconsistent width

polemidis, 2018-05-03:
For my initial setup I cut the gantry plates out of ½" plywood out of a CNC router, but plywood has flex and is not proper material for gantry plates.
The cad files have to reverted to the correct width, most likely ¼" which is sufficient for aluminum or garolite material

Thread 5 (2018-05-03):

The table dimensions need adjustment

polemidis, 2018-05-03:
We need to measure the actually cutting area, and depending what size is the parent material, to adjust the table dimensions. In US the minimum sheet metal comes to 4' × 8'

- [ ] Find references of minimimum sheet metal sizes

Either the table has to be longer or the Y rails need to be cut shorter, because they are not of the same length.

Closed 2018-08-21.

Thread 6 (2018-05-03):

Water table dimensions are wrong

polemidis, 2018-05-03:
- [ ] The water tables do not cover the whole bed currently. Make new version with water tables covering the whole bed.
- [ ] The thickness of the material in CAD is wrong, change it. Actual water beds should be made of 14ga not ⅛"

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

Closed 2018-08-21.

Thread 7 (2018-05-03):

Water table improvements

polemidis, 2018-05-03:
- A nice feature will be each bed to have a drain plug so the cutting fluid can be drained to a tank under the plasma table.

- A pump with individual valves for each water table can pump the water from the tank to the tables.

jurra, 2018-08-21:
- [ ] The water tables do not cover the whole bed currently. Make new version with water tables covering the whole bed.
- [ ] The thickness of the material in CAD is wrong, change it. Actual water beds should be made of 14ga not ⅛"

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

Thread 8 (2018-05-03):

Space management under the table

polemidis, 2018-05-03:
The space under the table should be utilized. Equipment that has to go under the table is:

1. The Plasma Cutter
2. The pump
3. The tank
4. A box with electronics for room for the power supply, for stepper drivers in case we need stronger ones, and for the breakout board. (for now the breakout board/stepper drivers are all in one and will be located at the end of the X drag chain on the top of the unused rail from X axis
5. Various tools

Some expanded metal on some 2" × ⅛" angle profiles should suffice.

jurra, 2018-05-22:
It is important to have size reference of equipment that needs to be placed below the table. It would be good to have an idea, and description of the prototype in pictures and examples of final products.

I put an example of plasma industrial plasma cutter
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

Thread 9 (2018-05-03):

Cable drag chains needed

polemidis, 2018-05-03:
The location of the X Axis drag chain is at the top of the 2nd rail at the X axis. CAD is needed

The Y axis drag chain location need to be designed. Most likely right under the right Y rail. but mounts have to be designed

jurra, 2018-05-22:
this one is repeated so I closed it. The other one has more content and comments.

Closed 2018-05-22.

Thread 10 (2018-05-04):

Torch Height Control

polemidis, 2018-05-04:
The Torch Height Control that is used is the [Proma Electronica SD](http://proma-elektronika.com/index.php/en/products/thc-torch-height-control/compact-thc-sd) and costs $300
I am dumb in electronics, but it should be easy to create a THC for a lot less.
The process is something along these lines:
The THC get input of the Arc Voltage of the Plasma, divide it 50:1, to a safe level for electronics, apply some filters, and then generate Step and Dir signals according to the voltage read. To high voltage means that the torch is too high, so step/dir signals that lower the Z axis are needed, and the opposite if too low voltage is measured.
If needed we can fast track this by reverse engineering my THC, or some research for other THC available is needed. There are also various plans on youtube, but are beyond my understanding :( I mean it I do not know much about electronics! :)

polemidis, 2018-05-22:
We can collect any THC resources from the net/youtube, and have them all here. So whoever gets involved with that, will have a better picture of what is needed and how its done by others

Witz0, 2018-08-21:
https://www.aliexpress.com/item/Highly-automated-tracking-Portable300-Arc-Voltage-Torch-Height-Controller-THC-Plasma-Height-Controller/32708675367.html

That is an example of less integrated older style electronics likely for a significantly different system. However, the circuit principles are the same. The separate THC is a good design for safety, modularity, and broad compatibility. The Proma THC manual states it has 1:50 divider, which confused me at first until I realized it is a standard option from the arc source and in addition to another HV divider within the THC itself.

The option from the source is probably better since it probably moves more of the components to the power source and they may be of better quality and give a cleaner signal to start. In that case any voltage divider and filtering on the THC side can be simpler, but this depends on details of that output from the source. Otherwise as the Proma manual states the THC needs HV/HF noise suppression for pilot arc then a HV divider, filtering, an arduino like MC with motor control outputs and optical isolation for safety and signal quality.

Another way may be to create a HV/HF noise suppression-voltage divider RC combo circuit with an opto-isolated ADC that outputs low voltage values back to the main arduino/RsbPi. This simplifies the circuit of the module that must be attached to the arc power supply. A possible con or issue is the arduino or RsbPi may then need to run more software emualtion like the PID currently on the modular THC to take the voltage inputs from the ADC and modify the Z controller outputs. This seems like a better more integrated solution, but grbl is optimized and likely designed to run on its own on the MC. Unless this can be neatly integrated it may cause problems with grbl. I'm currently uncertain of the RspbPi<-->Arduino I/O and if the RsbPi can assist in any way. A faster arduino version could also be an advanced complex option.

I'd guess advantages of moving THC complexity back to the main PCB might be more advanced control of THC functions, more accuracy at higher speeds, varying voltage target more accurately based on cornering speed, and by tracking wear on the consumable. But, given the likely software complexity involved keeping a dedicated MC for THC

Overall one of the most difficult parts is THC circuitry safety. It is critical because of the potential for a failure mode where arc power could enter the CNC side and come in contact with human interfaces. Thorough shielding and proper grounding of all PCB's and cables between them is critical to safety.

jurra, 2018-08-21:
From what I get here @Witz0 we are discussing different architecture options for electronics hardware. It would be nice to have a table to compare. It would be great to outline some requirements that sets criterion to make a proper decision.

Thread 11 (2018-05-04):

Screws have to be added (without threads)

polemidis, 2018-05-04:
All screws have to be added or at least measured in order to be able to provide a BOM

jurra, 2018-05-04:
- [ ] We have to count the screws
- [ ] And classify the different types of screws

polemidis, 2018-05-04:
I propose to replace the Z motor which is a Nema 17, with a Nema 23. The extra torque is not really needed but removes the need for these uncommon M3x45mm. The Nema 23 accepts M5.

jurra, 2018-05-04:
Do you think we are ready to start the BOM, wth the components we have? it would give a rough estimate of the cost right?

polemidis, 2018-05-04:
Yes we could add the more constant expenses leaving the variable ones for the end.
Can you investigate the market in europe for a plasma cutter that is NOT High Voltage, High Frequency start, but is a blowback or striking system pilot start? I do not know that market. If that helps, in the states a suitable plasma cutter which I have and also saw in videos, is the [Harbor Freight one](https://www.harborfreight.com/240-volt-inverter-plasma-cutter-with-digital-display-62204.html) for an entry level, the [Lotos cut60d](http://www.uwelding.com/supreme-cut60d-60amp-digital-control-cnc-non-touch-pilot-plasma-cutter-with-plasma-gouging-function-non-hf-blowback-arc-start-cnc-plasma-cutt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) for a better choice which hac already a 50:1 divider fro the THC, and on Hypertherm for the absolute industry workhorse (for double price :)
Anyway, that comment may be as an different issue for BOL

jurra, 2018-05-04:
Yes will take care of that

On Fri, May 4, 2018, 22:30 Manolis Karamousas <notifications@github.com>
wrote:

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

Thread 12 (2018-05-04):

Y axis Belt relocation?

polemidis, 2018-05-04:
I am wondering if it would be best to relocate the driving belt under the V-Slot® so it will be a) away from dirt and hot sparks. Right now it looks like dirt is piling on top of the belt, and is finding its way between the belt and the v-slot. Once is there is difficult to clean, the belt has to be removed and re-tighten.
That change only needs longer Y gantry plates as the motor will go below.

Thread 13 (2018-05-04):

Belt tightening system

polemidis, 2018-05-04:
Right now in order to tighten the belt these steps has be be followed:
a) the motor bolts have to be loose and the motor at the lowest position
b) the belt secured at the ends
c)the motor pulled up
d) while keeping the motor up, tighten the motor bolts.
But the motor bolts need two hands , one for the nut and one on the head with an allen key.

I propose to redesign the tightening process by making an adapter at the rail ends which will hold the belts tight, and then with a bolt along the long axis (direction of the belt)change the distance of the grabing location.  Its one extra item to be printed but worth the removal of the hassle to tighten the belt

polemidis, 2018-05-25:
This should suffice [](https://www.thingiverse.com/thing:1293079)

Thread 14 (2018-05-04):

Post processor needs to be wrighten

polemidis, 2018-05-04:
The function of the post processor is to add to or change the G-code that the CAM software generates in the specific machine's dialect.
Our CNC Plasma uses the minimal grbl g-code parser, and even though there are widely available post processors for the grbl, code have to be added to facilitate the
a) automatic Z axis zeroing with a floating table
b) ??

polemidis, 2018-05-08:
This is what I use so far.
G17
G90
G38.3 Z-100 F100 ; probing the Z
G0 L20 P1 Z-11 ;distance to raise. It "zeroes" the Z
G0 Z0 ; placing the torch at the Z distance to start firing

M3 S100000 ; ;torch start
G4 P0.6 ; delay, but it needs more

polemidis, 2018-05-09:
The line "G0 L20 P1 Z-11 " above, even though it works, is wrong. The number (-11) is mm (defined in G90) command, and the torch is definitely not 11m above the metal, but 1-2mm. When I troubleshouting the Z axis I messed up the steps/mm, most likely I have to recalculate the stepping

polemidis, 2018-05-22:
Closing this. Sheetcam haw a good post processor

Closed 2018-05-22.

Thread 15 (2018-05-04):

Spring tension to restore floating table

polemidis, 2018-05-04:
I created it in the prototype but have to make it in the CAD   ---Pictures needed---

instead of relying on the weight of the floating table+torch weight, a spring has to restore the floating table for reliability and stress free operation

jurra, 2018-05-22:
This is also a simple task right? finding a proper spring that works for the weight of the torch head. @polemidis correct me if I am wrong.

polemidis, 2018-05-23:
yeah pretty super easy. The weight is actually pulling to the same direction as the spring. But we cannot just count on the weight as dirt/friction etc my not be enough force to keep the torch head down. A small spring will do the job. I am satisfied with the rubber band it just look "cheap to the end user :)

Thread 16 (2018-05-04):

Cable management

polemidis, 2018-05-04:
- [ ] Maybe add to the CAD the Cable chains

- [ ] Design and add to the CAD the support for the Y axis (the long one) cable chain.

- [ ] Replace in CAD the top "threaded rod plate nema 23" (top plate on Z azis) with a longer one so the drag chain can attach there.

jurra, 2018-05-07:
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

jurra, 2018-05-18:
B=50mm width, 18mm height is the ones on the link i believe. Can you open it? The top where you measure the A should be removable so we frst put the wire in, and the close it. It will help 3D printing by a lot since so support is needed.

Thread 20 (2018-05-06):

New breakout board

polemidis, 2018-05-06:
One bottleneck in the assembly process of the machine is the hude delay in crimping wires so they can will have the the "Dupont connectors that the "CNC Shield"  that I use require. Its annoying and takes huge time.
We have to research for a new board that is compatible with the GRBL v1.1 software, and accepts the wires with no connectors, just simple screwed down.

polemidis, 2018-05-08:
One possible alternative is to replace the CNC shield with a similar board but for Raspberry Pi instead the Arduino. That approach even though it looks more expensive is actually a cheaper option as the Rasp. will replace the computer which runs the grbl sender program.
[CNC Board for Raspberry Pi](https://blog.protoneer.co.nz/raspberry-pi-cnc-board-hat/)

jurra, 2018-05-08:
Makes a lot of sense! then the user could talk to the raspberry pi in a home network for instance..

polemidis, 2018-05-09:
I have to double check (never had RPI) but if it can run Freecad, and Sheetcam (maybe the best CAM for plasma out there, in reasonable cost) then you just add a monitor/mouse/keyboard and you have your station ready.

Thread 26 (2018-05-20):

Task breakdown CNC torch table prototyping-testing-redesigning

jurra, 2018-05-20:
## Intro overview:
### We can put here an overview of what are the main tasks for this sprint, what are different problems that need to be solved, etc.  as a summary to guide contributors.

The CNC torch table has some issues that are short term oriented, and others mid term.
We are currently running a prototype test sprint, focused on finished the first working prototype. The sprint includes, the gathering of design recommendations, and updates for the CAD model and design documentation.

### Sprint goals:
1. Finish prototype tests and document enhancements needed
2. Modify the CAD files based on issues shared in the **[sprint board](https://github.com/goscommons/CNC-Plasma-Table/projects/3?fullscreen=true)**

Closed 2018-08-21.

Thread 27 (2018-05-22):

CNC test cut with grapples

jurra, 2018-05-22:
- [ ] What are key success criteria? quality of the cut? @polemidis is good to have a checklist or something that guides the documentation of the test
- [ ] Shut videos of the test

polemidis, 2018-05-22:
To be able to have clear cut pieces.
The variables that affect that is
a) Amperage (but for my low end plasma cutter is at 50Amps. It doesnot go more anyway. Ideally for 1/4" we would need 65Amps)
b) Speed
c) Cutting height
d) Piercing height

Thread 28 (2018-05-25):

Testing-Prototyping documentation of first prototype

jurra, 2018-05-25:
### I quote @polemidis from the chat

There are many things to capture from @polemidis reflections, for now I copied the chat.

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

> Whoever wants to read further, the stepper drivers I am using now, are the DRV 8825. The big drawback is that the user has to tweak their voltage with a screw and the max Amps they could deliver to the stepper motors was 1.5A without a cooling fan, 2.2A with a fan.
> The new ones will be the TB6600. 4Amps easy. No fan is needed, and the motors mount with screw-type connectors. Check them out. They are 10x more expensive than the DRV8825 but their cost is still insignificant $14 from usa, $6 shipped from china

Closed 2018-08-21.

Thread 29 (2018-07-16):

Use as much as possible same structural components (Table and structural parts)

jurra, 2018-07-16:
For the redesign of the table, we can use as much as possible same structural components. Alluminum profiles for the CNC frame and structural parts could be used to also fabricate the table.

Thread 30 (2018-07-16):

Kit Design of CNC Torch Table

jurra, 2018-07-16:
The general overview of the Kit Concept implies the following design goals:

1. To reduce transport costs, by providing the components, and sub-assemblies as compact as possible
2. To facilitate the assembly of the sub-assemblies and components for the user. Make the life easier for those who want to buy a kit and replicate the machine.
3. Make the tool head easy to exchange to convert the design into a router, a CNC laser cutter, or a Plasma cutter.

polemidis, 2018-07-16:
By saying different approach I actually mean complete redesign. Belts are not good enough to that size for router, so we are actually talking for a new machine. We have to clear this issue before continuing. Router is nice thing to have, but do we need it now? Personally I would love to have a router of that size ;) ;) but I have no time now to research a leadscrew type system

jurra, 2018-07-16:
The backlog items can be prioritized, if this is too complicated, or
unfeasible, we can take it to the bottom of the list, otherwise, maybe some
of us can take over this task.

On Mon, Jul 16, 2018 at 7:05 PM, Manolis Karamousas <
notifications@github.com> wrote:

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

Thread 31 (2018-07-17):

Product Backlog Documentation for a Kit design based on the current CNC prototype

jurra, 2018-07-17:
Here we document all the features, improvements and ideas for the new kit design. We are trying out Zenhub to use the scrum workflow.

The backlog may include sketches, ideas, and specific tasks as well.

JannesHN, 2018-07-24:
My idea of a kit of the CNC plasma cutter is that it only contains (relatively) small essential components.
Parts that we can buy in bulk, such as specific stepper motors, the microprocessor, the small elements in the gantries. The rest, the bigger parts such as the frame beams and rods for the x and y axis should be bought locally by the users.

vinaybhajantri, 2018-07-30:
Hey all, please see the general specifications list based on the small scale CNCs in the market. We should be able to determine these for our CNC too.

**Note**: I have already put sample values as an example

1. Standard workable area:  3,850 mm
2. Travelling capacity X axis:  3,850 mm without processing of the ends of profile
3. Travelling capacity Y axis:  350 mm
4. Travelling capacity Z axis:  280 mm
5. Fast feed Y - Z:  max. 30 m/min.
6. Fast feed X axis: 50 m/min.
7. Positioning accuracy: ± 0,1 mm
8. Spindle speed: 1-24,000 r.p.m.
9. Power output router spindle: 7,0 kW S1 with constant feedback torque control       
10. Tool support for 5 tools

jurra, 2018-08-21:
For now lets just keep the current specifications we have in the prototype and put them in the readme. Does it makes sense?

jurra, 2018-08-21:
## restructuring product backlog documentation:
I found many comments in separate issues, that can all be gathered here
Maybe this could also go on a seperate markdown file in the root folder of the repository

## Target requirements for CNC table
To be able to have clear cut pieces.
The variables that affect that is
a) Amperage (but for my low end plasma cutter is at 40Amps. It doesnot go more anyway. Ideally for 1/4" we would need 65Amps)
b) Speed
c) Cutting height
d) Piercing height

## Fabrication requirements
The whole machine should be able to be assembled on site.
This means using stockparts, machining and fastening with the leaast amount of different tools.

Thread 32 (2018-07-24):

BOM of the CNC as it is now

jurra, 2018-07-24:
- Plasma cutter selection related to the board.
- Plasma cutter thickness of sheets. 3mm sheet metals are the most common (Vinay did a check of suppliers in the Netherlands and Germany)
- Cost quality performance  for frames. Specify range of cost efficiency-

Specification range for aquisition of plasma cutter:
- How thick? maxtimum thickness?
- How much affects the range of cost (for frame design but also buying the plasma cutter).

JannesHN, 2018-08-02:
Here is a link to a Google sheet:
https://drive.google.com/open?id=1voFm5NLqLOZ_l4LTmCsCx7BCbBR0maWj1ovEqwTKXfg

It is a dynamic file for collaboration on the Bill of Materials to complete it together.
A static file will be made to keep track of the contributions over time and assure continuity .

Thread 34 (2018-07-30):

Update CAD file with new table frame

JannesHN, 2018-07-30:
When the frame design is updated from welded pieces to a modular design with standard extrusion profiles, a new CAD file must be made

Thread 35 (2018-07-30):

Design modular table frame

JannesHN, 2018-07-30:
A frame that is not a welded piece, but assembled from standard extrusion profiles

jurra, 2018-08-21:
The frame is already designed, is it properly validated?
Is it ready for a merge? or should we have it in the branch of new version that is not yet released?

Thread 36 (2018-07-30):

Grid that allow big and small shapes to be cutted

JannesHN, 2018-07-30:
The grid in the water tables, on which the sheet metals is placed, is decisive for the size of the shapes that can be cutted. Making a finer grid, that might be placed on top of the larger grid, allows for smaller shapes to be cutted by the machine.

polemidis, 2018-07-31:
I do not think so Jannes. The grid is decisive only on the parent material
that will be cut. Finer grid will make the cut more problematic and prone
to failure. I was already considering to remove the flat metals and replace
them with pyramid shapes, but other reasons like availability stopped me
from doing so

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

--
Emmanouil Karamousadakis
Certified Permaculture Designer
AGreekulture Farmstead
Winthrop, ME 04364

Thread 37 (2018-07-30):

Housing for the driver board

JannesHN, 2018-07-30:
In the prototype this is a plastic box. This can be a more tidy box that allows for neat cable management.

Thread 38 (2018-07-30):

Insert timing belt and belt assembly in CAD

JannesHN, 2018-07-30:
It sucks to make. But it will make the CAD design more complete and thus add to the clarity of the information on the design

polemidis, 2018-07-31:
Its not that hard. I already have made similar belt to the 3D printer
design on OSE printer. The only difference is the pitch. If noone else can
do it I will help

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

--
Emmanouil Karamousadakis
Certified Permaculture Designer
AGreekulture Farmstead
Winthrop, ME 04364

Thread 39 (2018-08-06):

Controller: with or without Raspberry Pi

JannesHN, 2018-08-06:
The following discussion took place on the control unit of the machine

**Manolis**
Did we decide? Arduino + CNC Shield or Raspberry Pi + CNC Hat + Monitor (with the later we can have the software already installed)

**Jannes**
Can both drive 4 steppers? Arduino's main benefit will be the price I guess, while the Raspberry Pi is more sturdy and can be more versatile when we start improving the design or adjusting it for other CNC purposes.
My preference goes out to the latter one, but it makes a huge difference in costs.

**Manolis**
Let me explain Jannes. The 1st choice is a CNC shield over an arduino. That has the regular (temporary) -non sturdy wire connections, and requires lots of labor intensive clamping of plugs.
The second choice is a CNC Hat that is running the arduino over a raspberry pi. The raspberry pi plays the role of a computer. Its benefits are that we can have the software already installed, it can be a complete solution as a stand alone CNC machine (no need to connect to another computer), and also has regular screw type connectors that save A LOT of time in clamping of delicate wires, and its more reliable/sturdy. The cost is not that much more, but the offer as a complete standalone system can gives as more money as a better product.

JannesHN, 2018-08-06:
Thanks for the explanation, but that does confirm for me that we should go with the Raspberry Pi included.
We want to shake off the DIY image of the machine, so having a more reliable complete product with the addition of a Raspberry Pi seems obvious.

polemidis, 2018-08-09:
I agree. Raspberry Pi with the CNC Hat, is better solution.

Closed 2018-08-09.

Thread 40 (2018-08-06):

Packaging design for kit

jurra, 2018-08-06:
## References for packaging design
https://www.ups.com/us/en/services/customized-solutions/optimization-logistics/package-engineering.page

jurra, 2018-08-06:
I had some experience with the packaging of a 3D printer kit. Some of the design of this packaging also applies to our context, specially for electronics, and components. They are the most vulnerable components.

## Question?
What about the plasma cutter, do we include it in the package or separatedly?

polemidis, 2018-08-09:
I am leaning towards a separate plasma cutter. different grid voltage/frequency accross the globe is hard to follow. I believe each customer has to buy its own plasma, while we can always suggest the models that we know that work in out countries.

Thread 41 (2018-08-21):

Repo restructuring with proper branches for different designs

jurra, 2018-08-21:
As @Witz0 correctly pointed, there are inconsistencies in documentation, specifically between BOM and current design. This is because the design is being improved, with a new table design that is more modular.

We have directly jumped into the redesign and improvement of the CNC plasma cutter, without clarifying that is a new version with very small change though.

To solve this we can:
- [ ] Merge the changes now (is the design of the new table sufficiently validated @JannesHN ?)
- [ ] Make the branch with v2, and make the changes in BOM for current version.

2nd option takes perhaps an effort that is does not worth it, and maybe we should treat this improvment with @JannesHN as our first official release.

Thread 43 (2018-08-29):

abnormal motions during cutting

Witz0, 2018-08-29:
[Plate with lines instead of arcs](https://files.gitter.im/goscommons-github-io/Lobby/aOJA/IMG_0490.JPG)
From the description it sounds like g-code commands or motion control errors that are inconsistent.

There are many possible causes so tracing this error could be difficult, but especially important if it is an unknown software error that affects all users and requires an issue to be submitted to another repo.

Without extensive knowledge of these systems, I can only think of a few possible causes from previous reading; mostly from the grbl wiki pages and issues:
https://github.com/gnea/grbl/wiki/Known-Issues

- Most likely is electrical interference, which can be chaotic in nature.
  - The [grbl repos](https://github.com/gnea) have many CNC builders' comments about such issues and it is especially significant on plasma systems due to the arc noise.
  - Reviewing [design issues photos](https://github.com/goscommons/CNC-Plasma-Table/tree/master/00_Design_Issues) shows some wiring details and the plastic boxes used to house the electronics.
  - The plastic is great for prototype work since it isolates potential shorts and is easy to rework. However, it also offers little or no shielding like metal would.

  - From the photos, it is unclear exactly what kind of cables and wires are used, but it does not appear to be shielded (poly fiber strands for riser cable type strain relief are visible).
    - Types of exterior grade plenum rated cables with foil shield and drain/ground wire are ideal for data signals outside a metal box.
      - Other considerations are twisted pair (TP) for differential signals (to THC),  stranded (patch) cable for flexibility;
      - unshielded cable with solid core wires can be used for jumpers between PCB's in screw terminals, but need to be in a shielded box;
      - Some Cat6 has plastic spline spacer (flexibility?) and Cat7 has separately shielded pairs.

  - Considering Pros/Cons of designs using a metal box for electronics may be critical.

    - A soild metal box should act as a faraday cage offering good shielding.
    - If used as chassis ground for electronics it must always be isolated from the + (plasma system ground) work circuit, which the table is apart of. User error such as bridging with metal parts is a potential problem.
    - Heat dissipation for a sealed metal box should be considered.
    - A metal box near the table but isolated from it could act as a fairly complete user interface.

- Next, see [USB serial transmission errors](https://github.com/gnea/grbl/wiki/Known-Issues#usb-to-serial-transmission-errors) in arduino clones and some official Arduinos the USB serial chip has bugs; the official ones have a firmware fix.

- Another common noise issue that introduces motion errors is [Wiring Limit Switches](https://github.com/gnea/grbl/wiki/Wiring-Limit-Switches). Many users add optically isolated limit switches to prevent noise from motors or plasma arcs feeding back as well as better software debouncing.

- A less likely issue now is incorrectly manufactured USB cables. A quick multimeter continuity test between both ends of the exterior plug chasis will tell if they bonded the sheilding to the cable ends correctly.
- Also, useful to know [arduino USB](http://forum.arduino.cc/index.php?topic=27226.msg201939#msg201939) spec appears to be v1.1 with max cable lengths of 9.8ft.

A good way to dry run the CNC system to test these errors would be ideal. Disabling the arc would be step one, but video of motions may be insufficient. Maybe a crude plotter (sprung pen/pencil) attachment could be (3D printed?) added to test g-code motions on paper taped to a metal sheet, but I'd guess this would require some software changes as well so expected signals can be ignored.

polemidis, 2018-08-29:
Its not a shielding problem. I am positive. I detected abnormal behavior only when there is a G2 movement (command "G2" on the g-code)
Statistically speaking it would be extremely rare to show up only in G2 moves (these are arcs).

But despite that, shielding is something we have to incorporate into the build, since it will eliminate possible errors to users. Its good to know that right now with unshielded wires, I have not noise in the machine, so one extra step in shielding will make 1000%  sure that we will never have to deal with that issue.

The solution to the G2 commands is either
a) tell the g-code generating software (sheetcam )to not use them
b) tell the g-code sender(universal Gcode sender) to transform the g2 arcs into small G1 straight lines before it sends it to the board
c) fine tune the accuracy on the Sheetcam. I have to experiment with the decimal points, and the rounding that is happening at some point.
d) make sure that Sheetcam uses the "Center Format Arc" rather than the "Radius Format"
[http://linuxcnc.org/docs/html/gcode/g-code.html#gcode:g2-g3](url)

The c) or/and d) looks like the proper way as the b) adds too much load to the processor and the a)also adds huge amounts of code.

jurra, 2018-08-29:
@Manolis Karamousadakis <polemidis@gmail.com> it would be also nice to
explain to Abe the difficulties you had wen using other open source
solutions. This is an issue that I don't know if is open in the repo at the
moment. But you basically went for sheetcam, to validate the hardware
design. The issue of finding an open source solution that works is still
open I guess.

On Wed, Aug 29, 2018 at 12:44 PM Manolis Karamousas <
notifications@github.com> wrote:

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

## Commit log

2018-05-03 Initial commit. Some files are deprecated
    [20 x 40 linear rail Z.fcstd, 8mm Leadscrew Acme 12in.fcstd, C beam X rail.fcstd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]
2018-05-04 added missing parts, but some assemblies broke need re-establishment
    [Aluminum Spacer .25in.step, Aluminum Spacer 20mm.step, Aluminum Spacer 9mm.step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]
2018-05-05 work on floating plate
    [Aluminum Spacer 20mm.fcstd, Aluminum Spacer 20mm.step, Aluminum Spacer 9mm.fcstd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]
2018-05-05 cable chain files added not yet in master cad
    [HD_Drag_Chain_End_V2.stl, HD_Drag_Chain_Start_V2.stl, HD_Drag_Chain_V2.stl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]
2018-05-05 housekeeping of the Y Rail Assembly
    [C beam X rail.fcstd, CNC Master CAD.fcstd, GT3 Timing Pulley 20T.fcstd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]
2018-05-06 remaking chains
    [HD_drag_Chain_V2.FCStd, chain-part.scad]
2018-05-06 chain-end freeCAD
    [HD_Drag_Chain_End_V2.FCStd, HD_drag_Chain_V2.FCStd]
2018-05-06 proper holes
    [HD_drag_Chain_V2.FCStd]
2018-05-07 rebuilding parts to make them adaptable and flexible
    [HD_Drag_Chain_End_V2.FCStd, HD_drag_Chain_V2.FCStd]
2018-05-07 Wider chain part
    [HD_drag_Chain_V2.FCStd]
2018-05-18 CableChain_Chain segment added
    Height is still wrong
    [UM2CableChain_ChainSegment.STL]
2018-05-18 Working out body interference and constrains
    This part we have to 3d print and test
    [Cable-chain-segment.FCStd]
2018-05-18 two walls
    [Cable-chain-chain-segment.FCStd]
2018-05-18 Added floor to cable chain
2018-05-18 Finished features of chain segment
    Fillets need to be added, and the links also must be softened.
    [Cable-chain-segment.FCStd]
2018-05-19 last version chain segment
2018-05-19 Model for printing
    Needs to be checked, before printing. The goal is to print the chain segment, and test, it with other chain segment, to see if its ready for replication.
2018-05-25 added support for cable chain
    [CNC Master CAD.fcstd, Drag Chain Y Axis Support Angles.fcstd, Drag Chain Y Axis Support Beam.fcstd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]
2018-05-26 added a complete chain on Y
    [Cable-chain-segment.FCStd, Chain Assembly Y.fcstd]
2018-05-26 added a complete chain master cad
    [CNC Master CAD.fcstd]
2018-05-26 added a chain to the master cad
    [CNC Master CAD.fcstd, Chain Assembly Y.fcstd]
2018-06-08 simplified folder structure
    [20 x 40 linear rail Z.fcstd, 8mm Leadscrew Acme 12in.fcstd, Aluminum Spacer .25in.step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]
2018-07-30 Initiated BOM
    Still in progress, in has link to Dutch webshops so that we can estimate the costs of a reproduction here.
    [CNC machine BOM.ods]
2018-08-16 Current BOM by jannes
    This is the complete BOM of Materials, including also the modular table frame designed made by jannes
    [Bill of Materials.ods]
2018-08-24 Bill of materials for current release
    This is the BOM of the current release of the CNC protype in use by @polemids
    [Bill of Materials.ods]
